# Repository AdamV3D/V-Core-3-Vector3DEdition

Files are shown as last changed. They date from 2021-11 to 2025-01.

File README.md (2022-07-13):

# V-Core-3-Vector3DEdition
Vector 3D Mods of the Rat Rig V-Core (3 & 3.1) 3D Printer with EVA

## General Change Goals
- improve printability especially for ABS. 
- printed parts to require no treatment after printing.
- screw insertion to never require force

## Common Changes
- Low layer chamfers changed from 45degrees to 63degrees. 
- Screw Hole diameter increased to be 0.5mm larger than Metric size. 
- Overhanging hole layer manipulation. 

## Print Settings
- Recommend ABS if possible, otherwise try Ooznest ABS Pro. Avoid esun abs+.
- I use 5 top, bottom and perimters
- 20-25% infill, gyroid or grid.
- 0.2mm layer height
- 0.4mm nozzle/line width

You can see more about my changes and mods to the V-Core 3 on youtube: https://youtube.com/playlist?list=PLWL37f39O8e8akqQdy8Pjt2n6UtyTdXjF

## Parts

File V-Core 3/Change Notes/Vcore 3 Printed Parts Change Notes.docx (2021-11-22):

# Vector 3D V-core Change Notes

## General Change Goals

- Aimed to improve printability, specifically for ABS
- Aimed for parts to require no treatment after printing
- Aimed for screw insertion to never require force

## Common changes across many parts

- Low layer chamfers changed from 45degrees to 63degrees
- Screw Hole diameter increased to be 0.5mm larger than Metric size
- Overhanging hole layer manipulation

## Rat Rig Parts

Lead Screw motor mount front

- Design adjusted to fix the bracket and adjust the motor.
- Increased hole size diameter
- Increased NEMA 17 hole size
- Extrusion slot alignment added

Passthrough nut

- Chamfers removed on one side.

Passthrough collar

- Chamfers on bottom face removed.

Cable Tie

- Number of segments reduced to improve build plate contact area.
- Smallest section of cable tie to grip reduced to improve grab on cables.
- Hole added to use 2.85 filament as cable strain relief

Y max endstop

- Slot size increased

Y max endstop block

- Hole size increased
- Printing face chamfers removed

Bed Arm Front & Rear

- MGN carriage hole sizes increased
- Lead screw block hole sizes increased
- Magnet hole sizes increased
- Magnet hole layer manipulation added
- Printing face chamfers removed.

Lead screw motor cage rear

- Design adjusted to fix the bracket and adjust the motor
- Mounting hole diameter increased
- Front mounting holes changed to slots
- Print face chamfers changed to 63 degrees
- Hole layer manipulation added
- Extrusion slot alignment added

XY Joiner L/R

- Changed design to not need large spacers
- Changed idler hole design to thru hole.
- Minor changes to chamfers to account for the above.

XY Idler

- Screw Hole size increased
- Overhanging hole layer treatment added
- Printed face over hanged changed to 63 degrees.
- Chamfer added to Y direction hole
- Chamfers added to vertical edges from printed face

Motor Cage top L/R

- Screw Hole size increased
- Overhanging hole layer treatment added
- Printed face over hanged changed to 63 degrees
- Chamfers added to vertical edges from printed face
- Sharp corners around NEMA mounting holes removed.

Motor Cage bottom L/R

- Screw Hole size increased
- Sharp corners around NEMA mounting holes removed

Pillow Block

- 63 degree angle added to printing face
- Screw hole size increased

Right Side Panel

- Truncated to allow assembly using partial side coverage

## EVA Parts

Dragon Shroud

- Hole size increased
- Overhang hole layer treatment added

Top Endstop Angled

- Low chamfers removed.
- Fillets replaced with chamfers

Universal Face

- Screw hole sizes increased
- Overhanging hole layer treatment added
- Low centre hex removed, nut moved to ‘Bottom – BMG, MGN, short duct’.
- Chamfers on hotend mounting face adjusted.

Dragon Face

- Screw how sizes increased
- Chamfer angles on printing faces reduced
- Chamfers around mounting face removed
- Layer treatment added to side hex holes.
- Top bridge thickness increased

Top – BMG, mgn12

- Top hex holes removed
- NEMA hole changed to flat top from printing face
- Hole sizes increased
- Zip tie holes added
- Connector holders added
- Additional strength added adjacent to NEMA

Back – BMG, MGN12

- Rear Logo size increased and text removed
- Recess added for fan clip
- Minor adjustments to chamfers to aid printing
- Nut clearances increased
- Chamfers added to lower duct holes
- Overhanging hole layer treatment added
- Screw hole sizes increased

Dragon V6 Support

- Changed from rear to side nut insertion
- Printing face chamfers increased to 63 degrees

Cable Holder – BMG

- Length increased
- Finger length reduced
- Cable tie grip diameter reduced
- Slot for 2.85mm filament strain relief added
- Print face contact area increased

Bottom – BMG, MGN12

- Zip tie holes removed
- Nut recess added (moved from universal front)
- Hole size increased

Universal Cable Mount – BMG

- Screw hole size increased
- Overhanging hole layer treatment added

## NEW Parts

Electrical

- Raspberry Pi Mounting Bracket
- 3030 Cable Clip
- Modified Lan Socket
- Modified IEC Socket
- WAGO 221 Block

Jigs

- 205mm Z Frame Spacer
- Lead Screw Alignment
- 47 & 43mm inner frame spacer

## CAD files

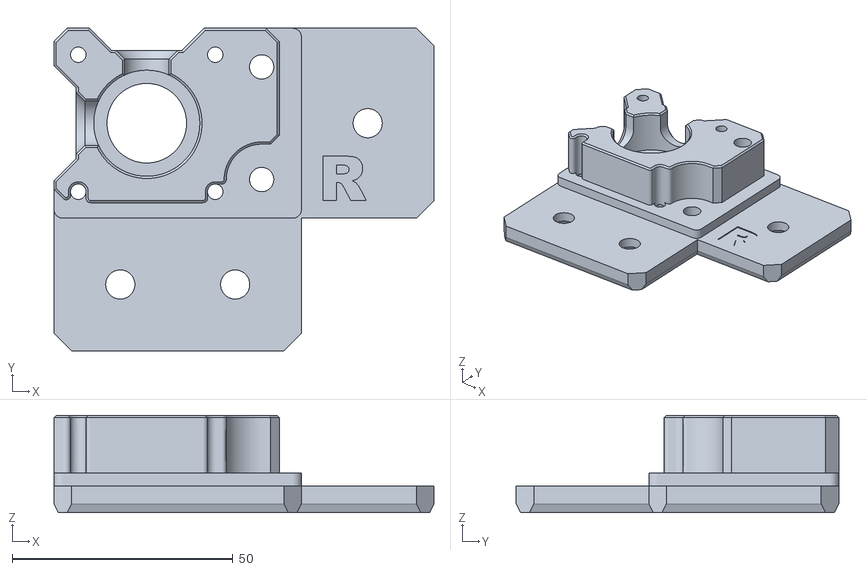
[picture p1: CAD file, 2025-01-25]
Enclosure 2.0/V3D_xy_motor_cage_top_right_3.1 ENC2 v1.stl
86.0 x 73.0 x 22.0

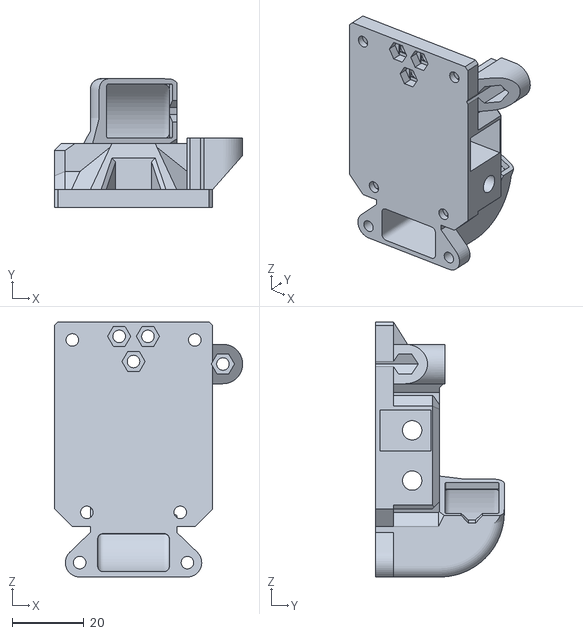
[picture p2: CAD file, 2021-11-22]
EVA 2/EVA/V3D EVA Back BMG CoreXY v21.stl
52.4 x 35.9 x 71.0

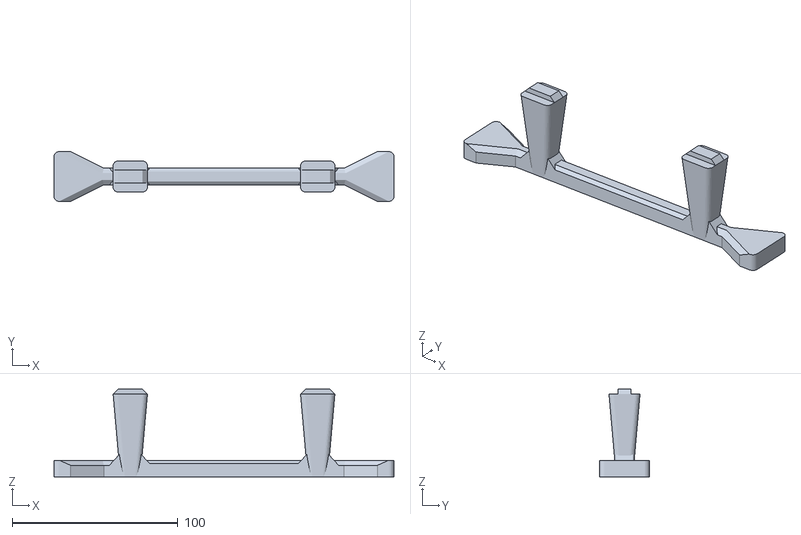
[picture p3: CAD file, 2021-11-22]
V-Core 3.1/Jigs/V3D 205mm Z Frame Spacer Jig v7.stl
205.0 x 30.0 x 53.0

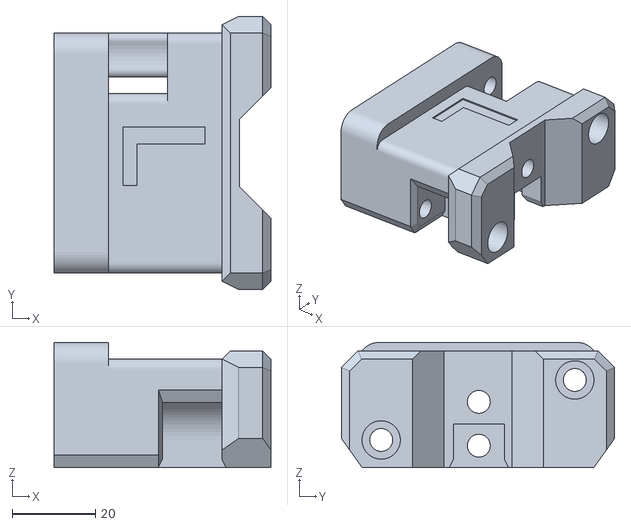
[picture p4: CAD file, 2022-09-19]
V-Core 3.1/Printer/V3D_xy_joiner_left_3.1 v12.stl
52.0 x 65.5 x 30.0

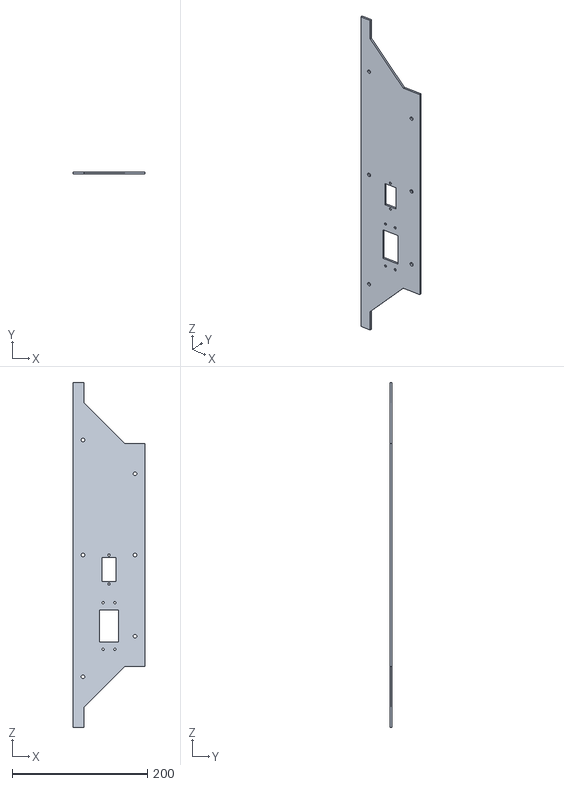
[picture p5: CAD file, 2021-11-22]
V-Core 3/Panels/V3D Side Panel Right Truncated v3.stl
107.0 x 3.00 x 510.0

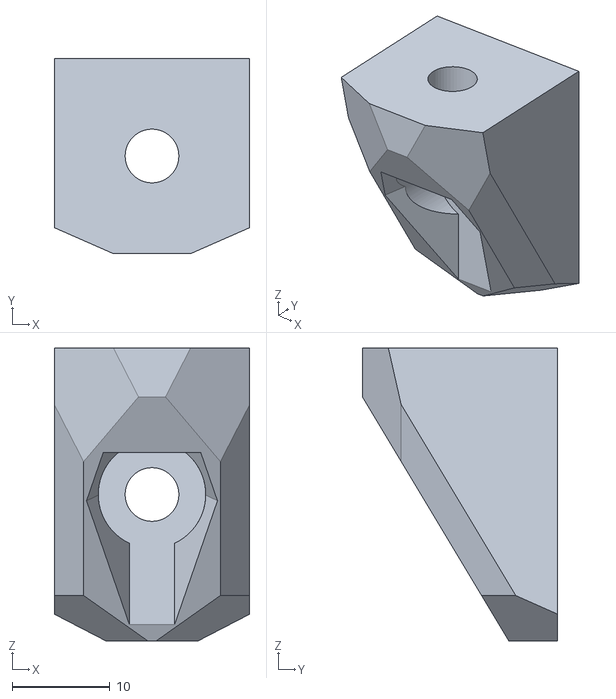
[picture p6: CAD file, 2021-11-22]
V-Core 3/Printer/V3D Y Max Endstop Block v4.stl
20.0 x 20.0 x 30.0

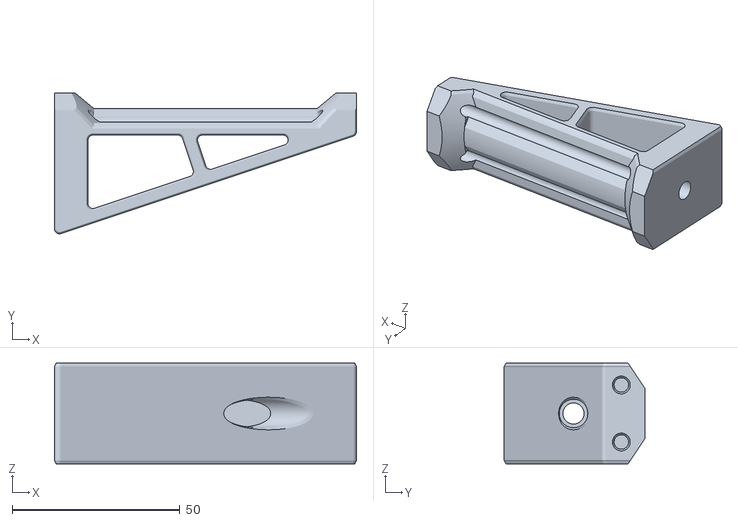
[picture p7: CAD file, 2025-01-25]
Enclosure 2.0/V3D Spool Holder With Enclosure v4.stl
90.0 x 41.9 x 30.0

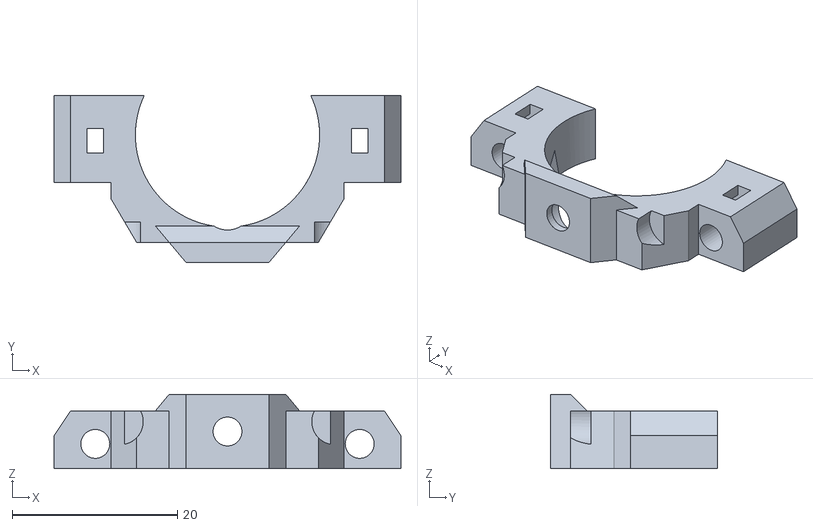
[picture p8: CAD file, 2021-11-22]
EVA 2/EVA/V3D EVA Dragon v6 Support v16.stl
42.0 x 20.2 x 9.00

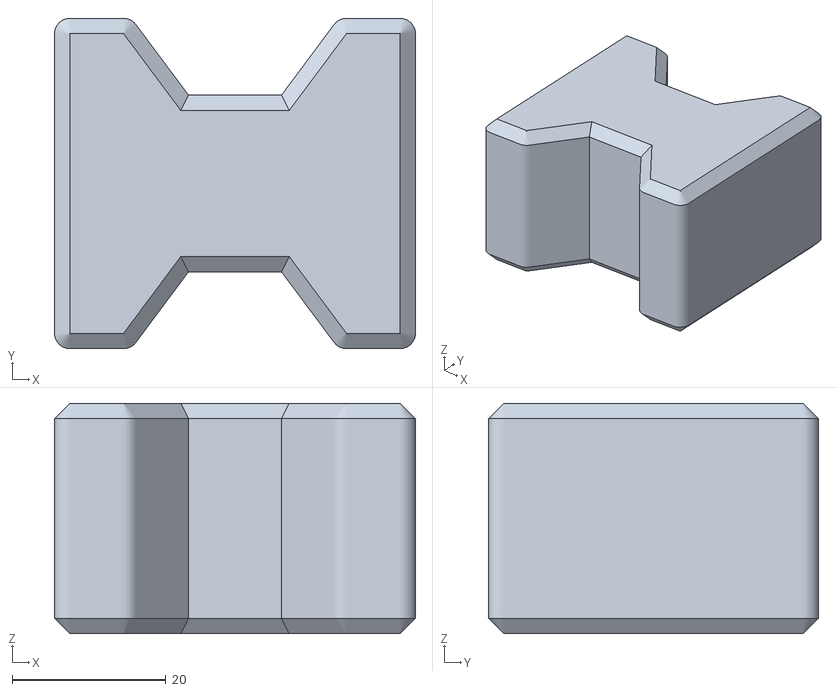
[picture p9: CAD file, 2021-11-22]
V-Core 3.1/Jigs/V3D 47 & 43mm Inner Frame Spacer Jig v7.stl
47.0 x 43.0 x 30.0

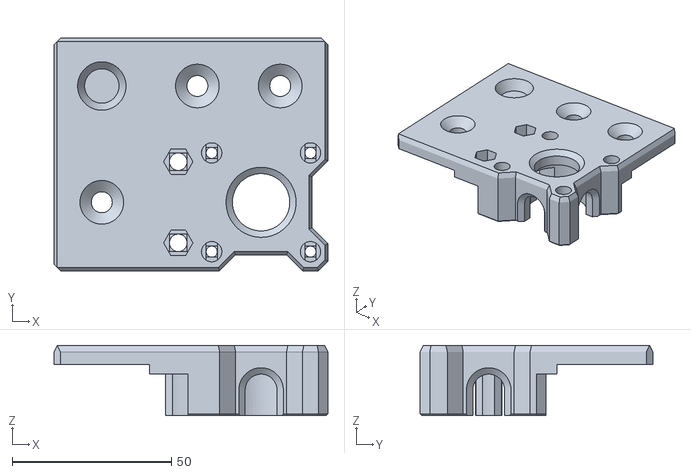
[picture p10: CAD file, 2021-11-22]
V-Core 3/Printer/V3D XY Motor Cage Top Left v7.stl
86.0 x 73.0 x 22.0

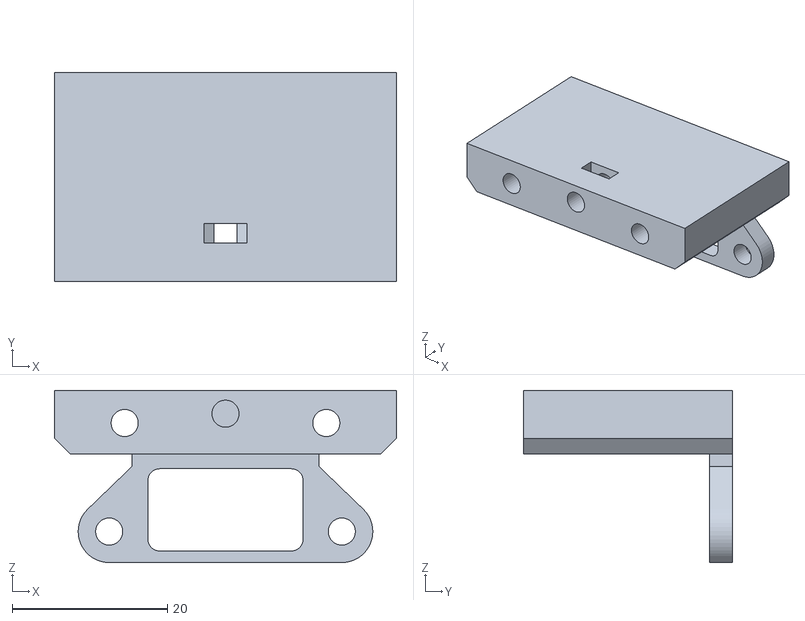
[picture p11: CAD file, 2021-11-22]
EVA 2/EVA/V3D EVA Bottom Short Duct MGN12 v5.stl
44.1 x 27.0 x 22.2

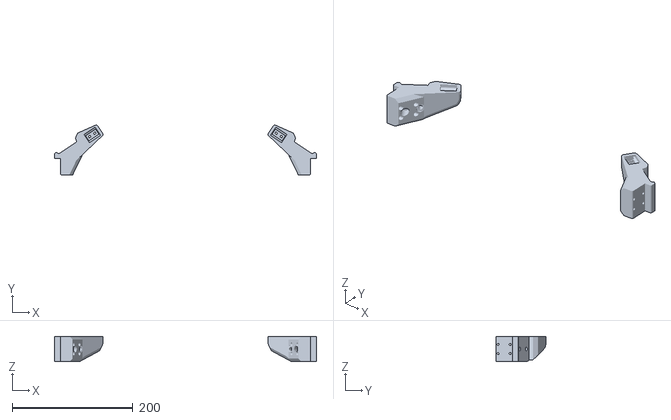
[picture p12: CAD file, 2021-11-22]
V-Core 3/Printer/V3D Bed Arms v5.stl
434.0 x 83.1 x 42.0

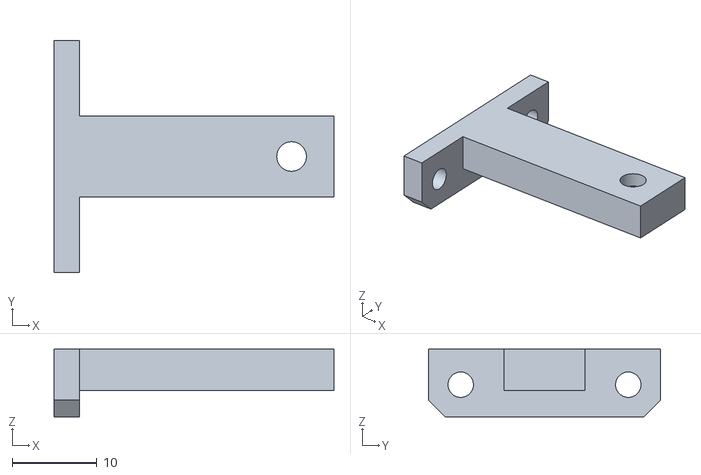
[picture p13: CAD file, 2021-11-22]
EVA 2/EVA/V3D EVA Top Endstop v2.stl
33.0 x 27.4 x 8.00

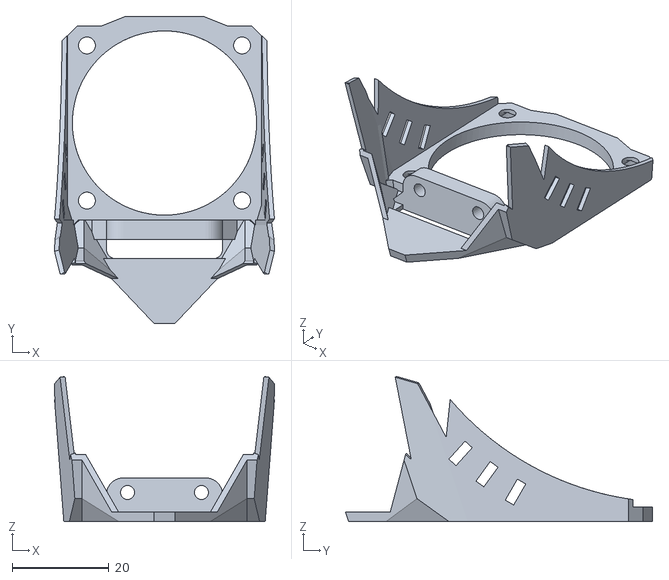
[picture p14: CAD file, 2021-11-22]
EVA 2/EVA/V3D EVA Dragon Shroud ADXL v7.stl
45.4 x 63.4 x 29.9

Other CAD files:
Enclosure 2.0/V3D_xy_motor_cage_top_left_3.1 ENC2 v1.stl
V-Core 3.1/Printer/V3D_xy_motor_cage_top_left_3.1 v6.stl
EVA 2/EVA/V3D EVA BMG Universal Face v13.f3d
EVA 2/EVA/V3D EVA BMG Universal Face v13.stl
EVA 2/EVA/V3D EVA Back BMG CoreXY v21.f3d
EVA 2/EVA/V3D EVA Bottom Short Duct MGN12 v5.f3d
EVA 2/EVA/V3D EVA Cable Holder v11.f3d
EVA 2/EVA/V3D EVA Cable Holder v11.stl
EVA 2/EVA/V3D EVA Dragon Face v24.f3d
EVA 2/EVA/V3D EVA Dragon Face v24.stl
EVA 2/EVA/V3D EVA Dragon Shroud ADXL v7.f3d
EVA 2/EVA/V3D EVA Dragon Shroud v1.f3d
EVA 2/EVA/V3D EVA Dragon Shroud v1.stl
EVA 2/EVA/V3D EVA Dragon v6 Support v16.f3d
EVA 2/EVA/V3D EVA Top BMG MGN12 v16.f3d
EVA 2/EVA/V3D EVA Top BMG MGN12 v16.stl
EVA 2/EVA/V3D EVA Top Endstop v2.f3d
EVA 2/EVA/V3D EVA Universal Cable Guide v4.f3d
EVA 2/EVA/V3D EVA Universal Cable Guide v4.stl
V-Core 3.1/Jigs/V3D 205mm Z Frame Spacer Jig v7.f3d
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

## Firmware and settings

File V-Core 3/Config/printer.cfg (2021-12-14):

## DO NOT EDIT THIS FILE, IT IS A TEMPLATE.
# Rat Rig V-core 3 Klipper Config

# The first thing you'll need to do is go through this file and comment out / uncomment 
# the files and/or settings you need.
# You'll be able to print just fine with this config as it is, but it is recommended
# that you follow these steps to properly calibrate your printer:
# 0) Sanity check and PID Tuning: https://www.klipper3d.org/Config_checks.html
# 1) Pressure Advance: https://www.klipper3d.org/Pressure_Advance.html
# 2) Skew Correction: https://www.klipper3d.org/skew_correction.html
# 3) Resonance Compensation: https://www.klipper3d.org/Resonance_Compensation.html

# Read more about klipper here: https://www.klipper3d.org/Overview.html

### CONTROL BOARD
#[include config/boards/btt-skr-pro-12/config.cfg]
[include config/boards/btt-octopus-11/config.cfg]


### BASE SETUP
[include config/printers/v-core-3/v-core-3.cfg]
[include config/printers/v-core-3/steppers.cfg]
[include config/printers/v-core-3/tmc2209.cfg]

### Stepper mechanical overrides
[stepper_x]
dir_pin: x_dir_pin # Add ! in front of pin name to reverse X stepper direction
rotation_distance: 40 # 40 for 20 tooth 2GT pulleys, 32 for 16 tooth 2GT pulleys

[stepper_y]
dir_pin: y_dir_pin # Add ! in front of pin name to reverse Y stepper direction
rotation_distance: 40 # 40 for 20 tooth 2GT pulleys, 32 for 16 tooth 2GT pulleys

[stepper_z]
dir_pin: !z0_dir_pin # Add ! in front of pin name to reverse Z stepper direction
rotation_distance: 4 # 4 for TR8*4 lead screws

[stepper_z1]
dir_pin: !z1_dir_pin # Add ! in front of pin name to reverse Z1 direction
rotation_distance: 4 # 4 for TR8*4 lead screws

[stepper_z2]
dir_pin: !z2_dir_pin # Add ! in front of pin name to reverse Z2 direction
rotation_distance: 4 # 4 for TR8*4 lead screws

[extruder]
dir_pin: !e_dir_pin # Remove ! in front of pin name to reverse extruder direction

# Uncomment this next line if you have an ADXL345 connected to the SKR PRO
[include config/sensors/adxl345.cfg] 

### HOMING
# BL Touch
[include config/z-probe/bltouch.cfg]
[bltouch]
z_offset: 2.55 # Adjust this to fit your setup

# Inductive/Capacitive probe
#[include config/z-probe/probe.cfg]
#[probe]
#z_offset: 0.0 # Adjust this to fit your setup
#pin: ^!probe_pin # Change this to suit your probe (NPN/PNP NO/NC) if necessary.

# Physical endstops
[include config/printers/v-core-3/physical-endstops.cfg]
[safe_z_home]
home_xy_position: 150,150 # 300mm printer
#home_xy_position: 200,200 # 400mm printer
#home_xy_position: 250,250 # 500mm printer

# Endstop position
# Adjust this to your setup
# Note: might need fine tuning.
[stepper_y]
position_endstop: 300  # 300mm printer
#position_endstop: 400 # 400mm printer
#position_endstop: 500 # 500mm printer
[stepper_x]
position_endstop: 0

# Sensorless homing (Beware: this requires manual tinkering and does not work if your x/y stepper drivers
# have clipped DIAG pins). It is strongly encouraged to use physical endstops if you're a beginner.
# If you still wish to proceed, copy config/templates/sensorless-homing.cfg to the root directory and 
# remove the # from the line below.
#[include sensorless-homing.cfg]

### PHYSICAL DIMENSIONS
# Remove the # from your printer size below. 
# Similarly add a # in front of [include config/printers/v-core-3/300.cfg] if you have a bigger machine.
[include config/printers/v-core-3/300.cfg]
#[include config/printers/v-core-3/400.cfg]
#[include config/printers/v-core-3/500.cfg]

### SPEED & ACCEL
# Acceleration
# Check https://www.klipper3d.org/Resonance_Compensation.html for input shaper calibration.
#[include config/printers/v-core-3/speed-limits-basic.cfg]
# Do not enable this next line without actively cooled stepper drivers.
[include config/printers/v-core-3/speed-limits-performance.cfg]


### EXTRUSION

# Extruder
[include config/extruders/bmg.cfg]
# [include config/extruders/lgx.cfg]
# [include config/extruders/orbiter.cfg]
# [include config/extruders/hemera.cfg]
# [include config/extruders/titan.cfg]

# Hotend
# [include config/hotends/v6.cfg]
# [include config/hotends/copperhead.cfg]
# [include config/hotends/mosquito.cfg]
# [include config/hotends/mosquito-magnum.cfg]
# [include config/hotends/dragon-standard-flow.cfg]
[include config/hotends/dragon-high-flow.cfg]

# Pressure Advance
# Check https://www.klipper3d.org/Pressure_Advance.html for pressure advance tuning.
[extruder]
#pressure_advance: 0.05

### HOTEND HEATING
# PID Tuning (Remember to run PID tuning before printing)
#control: pid
#pid_kp: 28.413
#pid_ki: 1.334
#pid_kd: 151.300

### BED HEATING
# BED PID Tuning (Remember to run PID tuning before printing)
[heater_bed]
#control: pid
#pid_Kp: 22.2
#pid_Ki: 1.08
#pid_Kd: 114

### MACROS
[include config/macros.cfg]
[include config/printers/v-core-3/macros.cfg]


### USER OVERRIDES
# Place all your overrides here
[bltouch]
stow_on_each_sample: False
probe_with_touch_mode: True

[bed_mesh]
speed: 100
probe_count: 6,6

[safe_z_home]
speed: 100
z_hop: 25

#controller fan
[controller_fan controller_fan]
##	Controller fan - CNC_FAN2
pin: fan_controller_board_pin
fan_speed: 1.0
#max_power: 0.8
shutdown_speed: 1.0
kick_start_time: 0.5
heater: heater_bed

#led lighting
[output_pin caselight]
#Chamber Lighting - HE1 Connector (Optional)
pin: PA3
pwm:true
shutdown_value: 0
value:0.1
cycle_time: 0.0025

[z_tilt]
points:
	60,270
	185,60
	260,270

[printer]
max_accel: 5100 #minimum of Y and X for IS.

[skew_correction]

[gcode_macro START_PRINT]
gcode:
  SAVE_GCODE_STATE NAME=start_print_state
  G21 ;metric values
  G90 ;absolute positioning
  M82 ;set extruder to absolute mode
  G28 ;home
  M117 Heating...
  M190 S{params.BED_TEMP|default(printer.heater_bed.target, true) }; wait for bed to heat up
  M109 S150 ; Wait for extruder to reach 150 so an inductive probe (if present) is at a predictable temp. Also allows the bed heat to spread a little.
  Z_TILT_ADJUST ;Adjust bed tilt
  G28 Z ;Home again as Z will have changed after tilt adjustment and bed heating.
  BED_MESH_CALIBRATE PROFILE=vcoreos ; Calibrate bed mesh
  BED_MESH_PROFILE LOAD=vcoreos
  SKEW_PROFILE LOAD=my_skew_profile
  G28
  G0 X{printer.toolhead.axis_maximum.x / 2} Y{printer.toolhead.axis_maximum.y} Z50 F6000 ; Park in the back and wait for extruder
  M109 S{params.EXTRUDER_TEMP|default(printer.extruder.target, true) }; wait for extruder to heat up
  M117 Printing...
  RESTORE_GCODE_STATE NAME=start_print_state
  M82
  G92 E0

[gcode_macro _END_PRINT_AFTER_HEATERS_OFF]
gcode:
  # Calculate safe Z position
  {% set max_z = printer.toolhead.axis_maximum.z|float %}
  {% set act_z = printer.toolhead.position.z|float %}
  {% if act_z < (max_z - 2.0) %}
      {% set z_safe = 2.0 %}
  {% else %}
      {% set z_safe = max_z - act_z %}
  {% endif %}
  # Relative positioning
  G91
  # Retract the filament a bit before lifting the nozzle.
  G1 E-2 F3600
  # Move to safe Z position
  G0 Z{z_safe} F3600
  # Retract filament even more
  G1 E-8 F3600

#*# <---------------------- SAVE_CONFIG ---------------------->
#*# DO NOT EDIT THIS BLOCK OR BELOW. The contents are auto-generated.
#*#
#*# [extruder]
#*# control = pid
#*# pid_kp = 24.688
#*# pid_ki = 1.228
#*# pid_kd = 124.055
#*#
#*# [heater_bed]
#*# control = pid
#*# pid_kp = 58.633
#*# pid_ki = 2.458
#*# pid_kd = 349.600
#*#
#*# [bed_mesh default]
#*# version = 1
#*# points =
#*# 	0.052213, -0.004037, 0.020963, 0.044713, 0.004713, -0.001537
#*# 	-0.006537, -0.005287, 0.012213, 0.035963, -0.011537, -0.012787
#*# 	-0.035287, -0.019037, 0.005963, 0.015963, -0.037787, -0.025287
#*# 	-0.024037, -0.005287, 0.033463, 0.020963, -0.022787, -0.007787
#*# 	-0.019037, -0.006537, 0.038463, 0.052213, -0.007787, 0.010963
#*# 	0.004713, 0.032213, 0.089713, 0.115963, 0.053463, 0.047213
#*# tension = 0.2
#*# min_x = 20.0
#*# algo = bicubic
#*# y_count = 6
#*# mesh_y_pps = 2
#*# min_y = 20.0
#*# x_count = 6
#*# max_y = 260.0
#*# mesh_x_pps = 2
#*# max_x = 265.0
#*#
#*# [input_shaper]
#*# shaper_type_x = mzv
#*# shaper_freq_x = 61.6
#*# shaper_type_y = 2hump_ei
#*# shaper_freq_y = 67.8
#*#
#*# [skew_correction my_skew_profile]
#*# xy_skew = -0.00851381161043
#*# xz_skew = 0.0
#*# yz_skew = 0.0

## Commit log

2021-11-22 Initial Commit of all modifications made to V-Core 3 up to this date
    see change notes document
    [EVA BMG_BMG_Extruder v1.f3d, EVA BMG_BMG_Extruder v1.stl, EVA BMG_NEMA17 v1.f3d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]
2021-11-22 Removed non modified and testing parts
    [EVA BMG_BMG_Extruder v1.f3d, EVA BMG_BMG_Extruder v1.stl, EVA BMG_NEMA17 v1.f3d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]
2021-12-14 Config File Added
    [printer.cfg]
2022-05-24 added print settings to readme
2022-07-13 V-Core 3.1 Printer Parts Added
    [V3D 205mm Z Frame Spacer Jig v7.f3d, V3D 205mm Z Frame Spacer Jig v7.stl, V3D 47 & 43mm Inner Frame Spacer Jig v7.f3d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]
2022-09-19 Left XY Idler bearing Stack space fixed
    There was an issue where the space for one of the bearings stacks on the Left XY Joiner was 0.5mm too small. This has been fixed to match the spacing for the 3 other bearing stacks. V11 removed, V12 added
    [V3D_xy_joiner_left_3.1 v11.f3d, V3D_xy_joiner_left_3.1 v11.stl, V3D_xy_joiner_left_3.1 v12.f3d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]
2025-01-25 cage update
    [V3D Spool Holder With Enclosure v4.stl, V3D_xy_motor_cage_top_left_3.1 ENC2 v1.stl, V3D_xy_motor_cage_top_right_3.1 ENC2 v1.stl]
